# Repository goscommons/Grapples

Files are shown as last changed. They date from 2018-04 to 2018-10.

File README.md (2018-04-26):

# Welcome to this open source project
This repository has specific structure inspired in the [open hardware repository project structure guidelines](https://www.ohwr.org/projects/ohr-support/wiki/project-structure-guidelines). It has been also provided and organized by GO!Commons a community and initiative focused on the role of open source to accelerate sustainable development and deliver economic empower to producers, and commoners.

## About the structure and organization of the repository
The wiki is a very important part of the documentation structure of this repo. It will give you a quick introduction to the particularities of this design, how it is used, how it works, why it exists, but also the functional description of it etc.
### For users
If you are interested in understanding how this machine/product works, you can learn from reading the documentation. If you want to use the files in your projects, and make your own redesigns you are also welcome. Make sure to read the rights and attributions you have as a user in the [LICENSE.md](LICENSE.md).

### For contributors
If you want to learn open source by doing things, and you are interested in participating in this project in particular. Contact us or leave a comment on the #issues you are interested in participating. Some issues are for advanced developers others, are for beginners.

**don't be shy, we encourage that people partner up, and we also promote that experienced people play a mentor role so that others can grow as well**

#### You can see the different roles in the GO!Commons canvas, where we lay out the different roles that can participate. If you think your role is not captured or expressed, also feel free to reach out. You can also select the one that you fill more close to and start learning and finding your own contributor profile along the way.
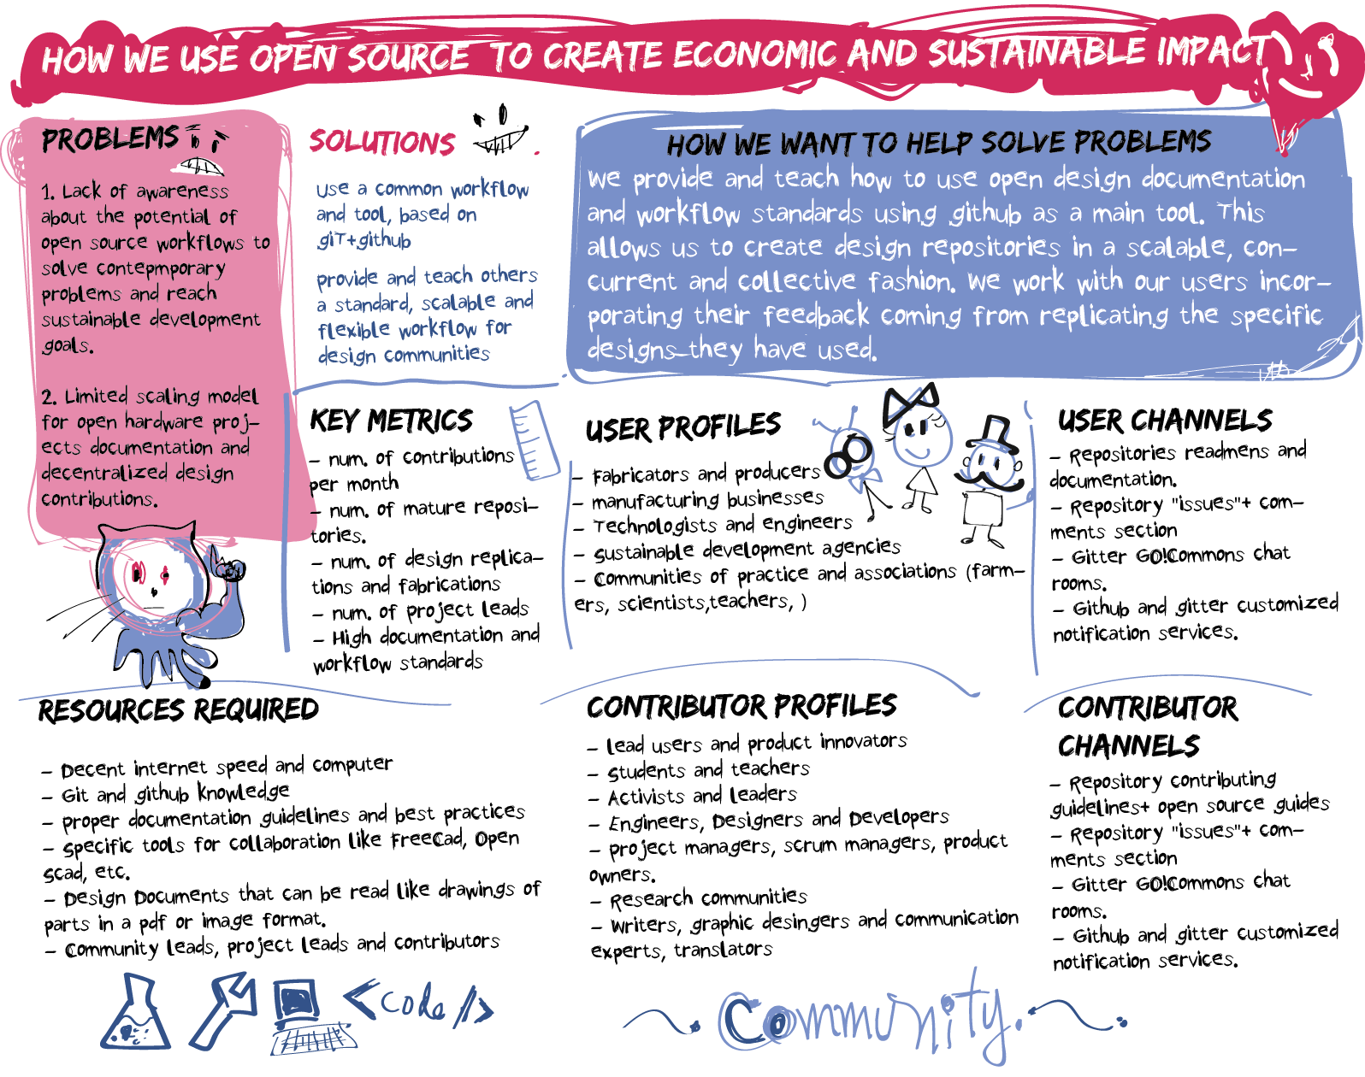
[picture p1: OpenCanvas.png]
GO!Commons Canvas


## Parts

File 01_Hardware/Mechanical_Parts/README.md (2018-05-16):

## What is the content in this folder and how to use it
The CAD structure is a diagram that allows you to understand different aspects of the design including:
* Dependencies and relations between parts.
* Fabrication related information like which parts will be manufactured with what process.
* Assembly and subassembly structures, very important to understand how to replicate the machine.
#[Find the link to the diagram here](https://drive.google.com/file/d/1CbiELoN1rX2ZCeMyn5z_mOmvfSASwcS_/view?ts=5af6c786). This will teach you how to also do similar kinds of diagrams.

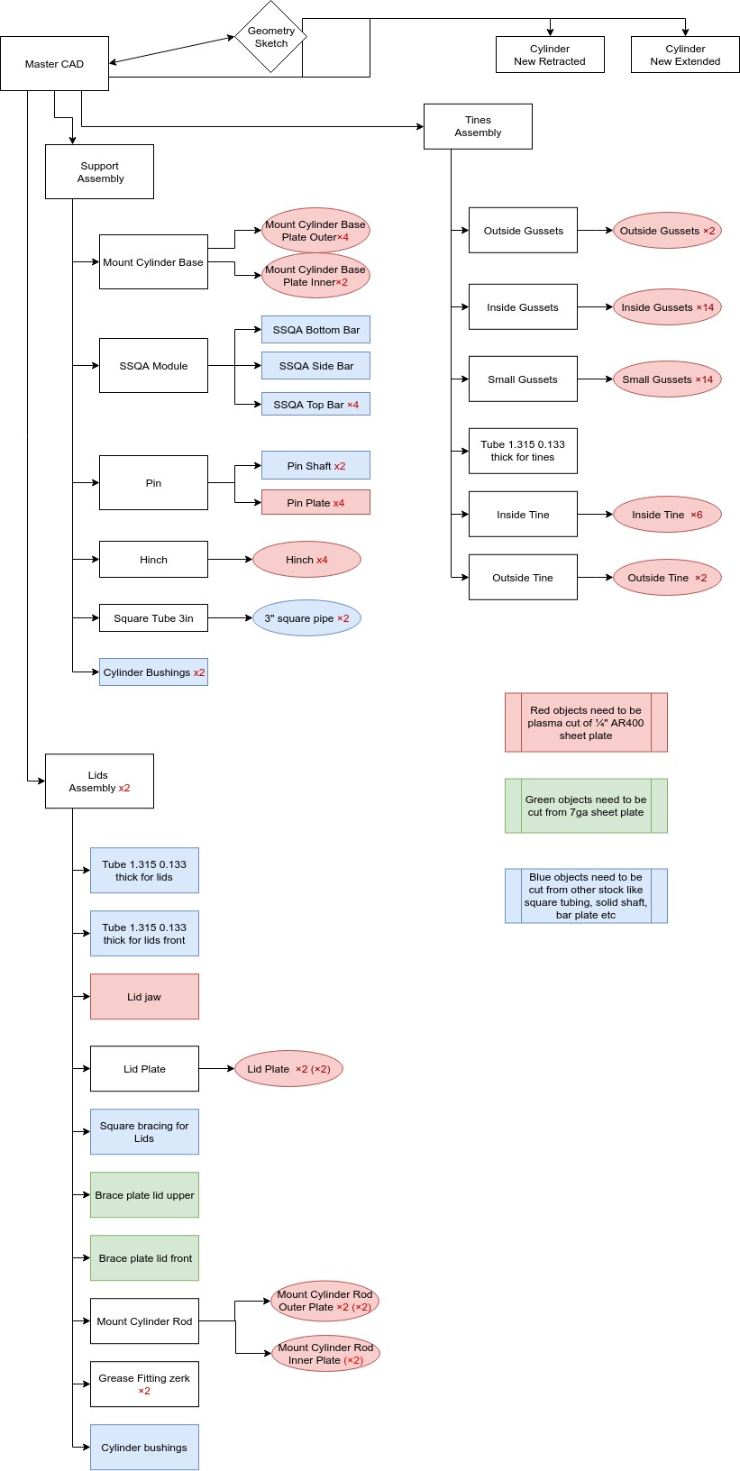
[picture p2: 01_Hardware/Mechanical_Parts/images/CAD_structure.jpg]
cad structure


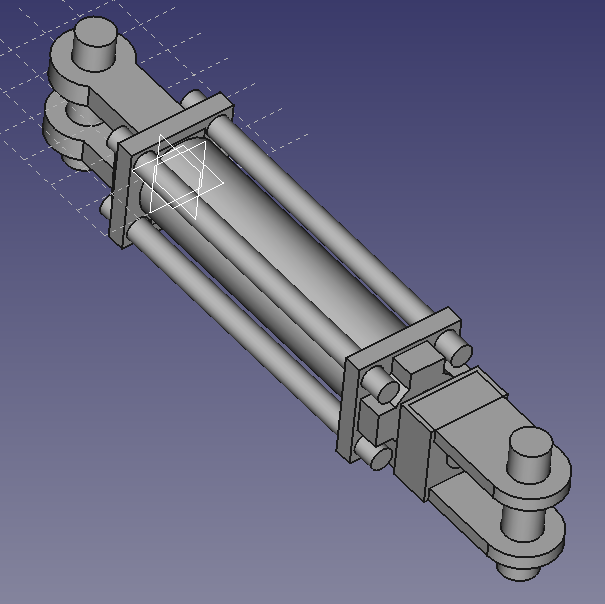
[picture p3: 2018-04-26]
01_Hardware/Mechanical_Parts/images/cylynder_retracted.png

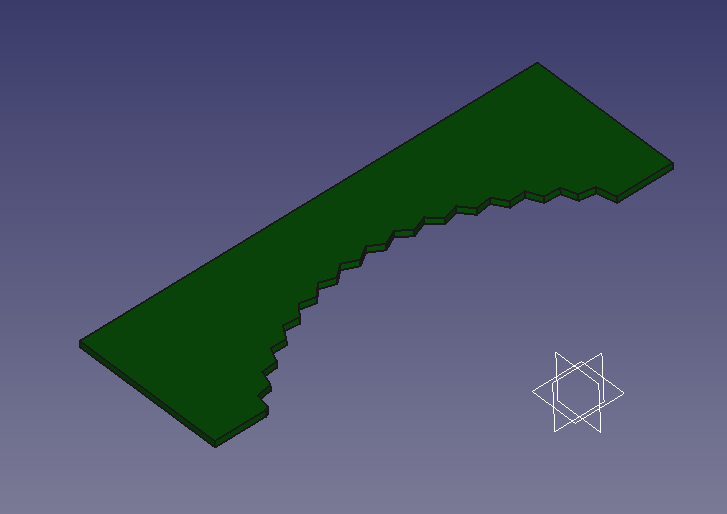
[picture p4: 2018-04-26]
01_Hardware/Mechanical_Parts/images/lid_jaw.png

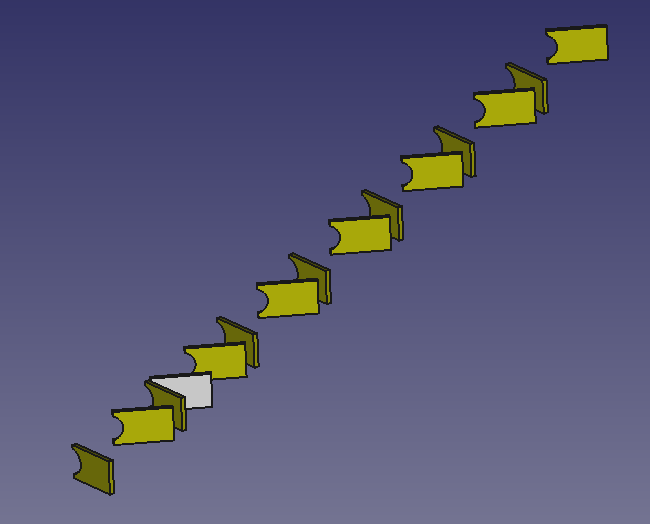
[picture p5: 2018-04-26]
01_Hardware/Mechanical_Parts/images/gussets.png

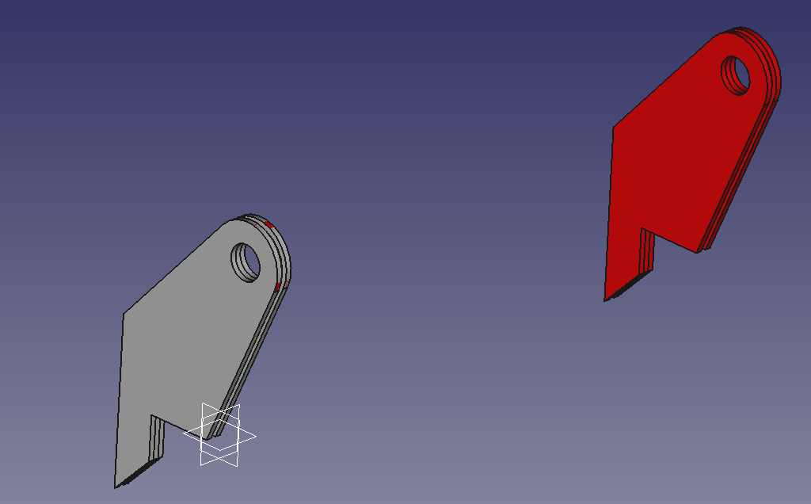
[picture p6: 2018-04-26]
01_Hardware/Mechanical_Parts/images/cylinder_base_mount.png

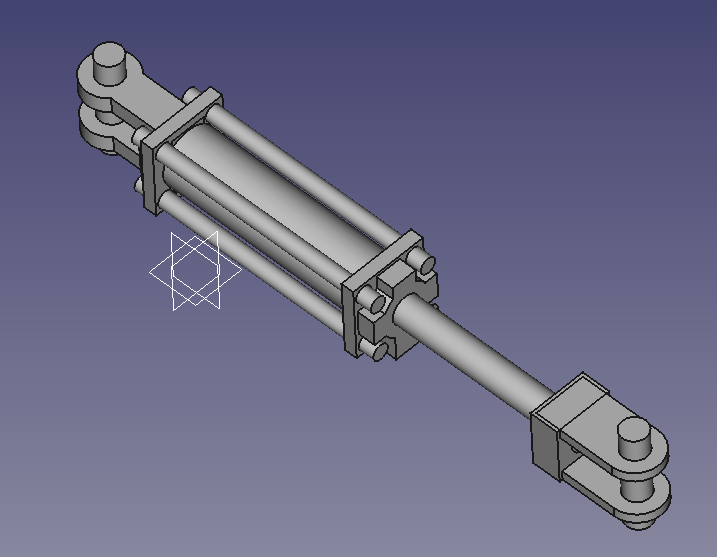
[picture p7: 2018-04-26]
01_Hardware/Mechanical_Parts/images/cylynder_extended.png

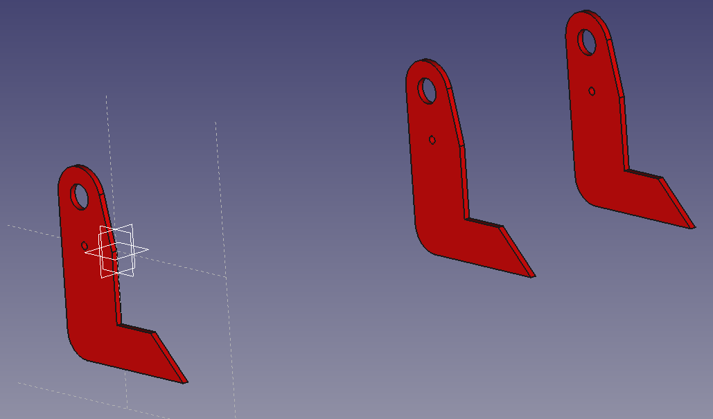
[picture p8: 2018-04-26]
01_Hardware/Mechanical_Parts/images/hinch.png

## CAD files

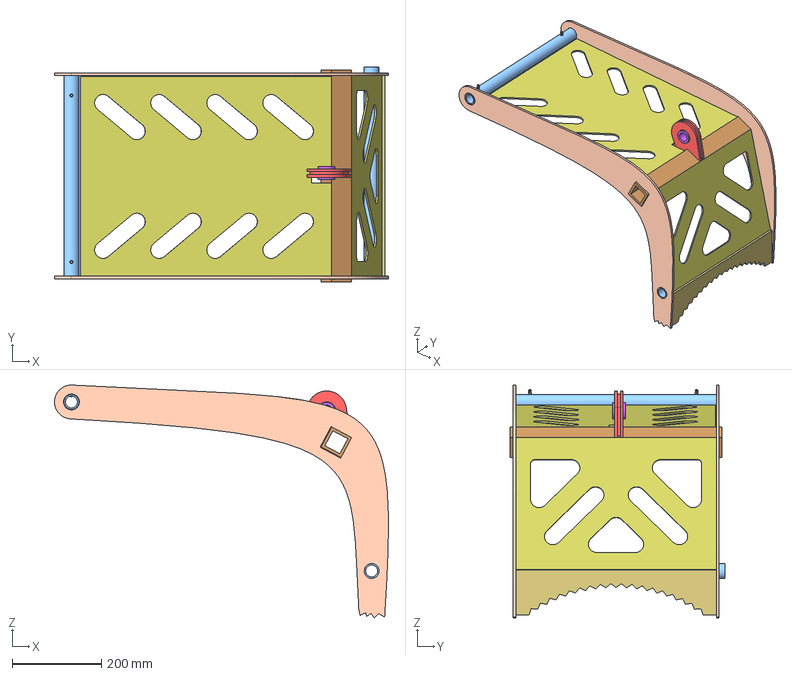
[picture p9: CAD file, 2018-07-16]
01_Hardware/Mechanical_Parts/CAD/Lids Assembly.fcstd
750.5 x 482.6 x 523.4 mm
Lid_jaw_01
Tube_1_315_0_133 thick_for_lids_01
Lid_Plate_01
Tube_1_315_0_133 thick_for_lids_front
Square_bracing_for_lids_01
brace_plate_lid_upper_01
brace_plate_lid_front_01
Cylinder_rod_mount_01
grease_fitting_zerk_01
grease_fitting_zerk_02
cylinder_bushings_01

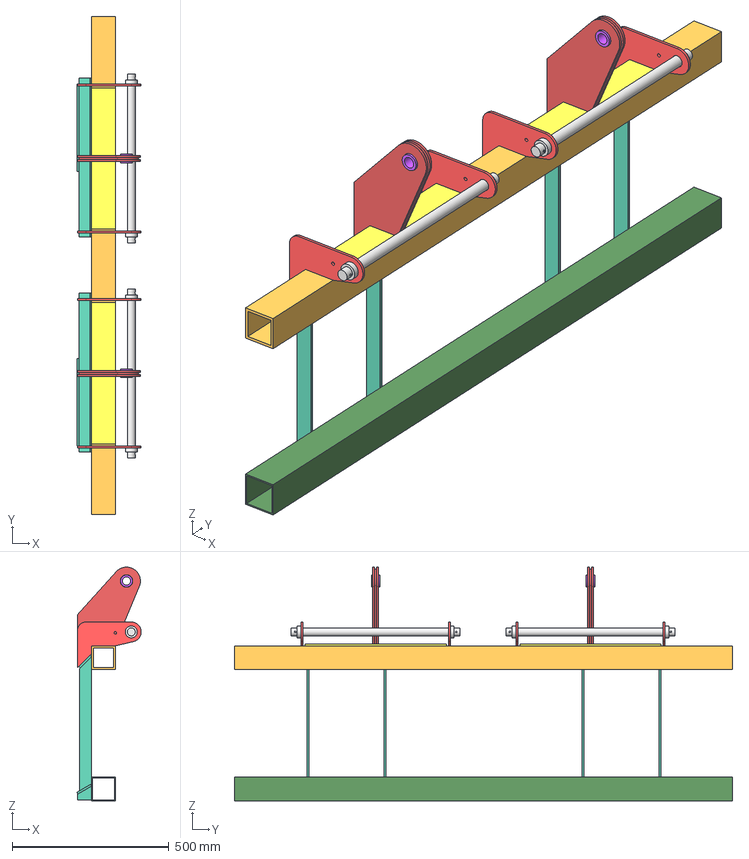
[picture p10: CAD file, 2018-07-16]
01_Hardware/Mechanical_Parts/CAD/Support Assembly.fcstd
205.9 x 1590.5 x 746.8 mm
mount_cylinder_base_01
ssqa_module_01
hinch_01
Square_tube_3in_01
bushings_for_cylinder_01
bushings_for_cylinder_02
pin_module_01
pin_module_02
Square_tube_3in_bottom_01
Support_plate_on_top_of_square_tubing_01

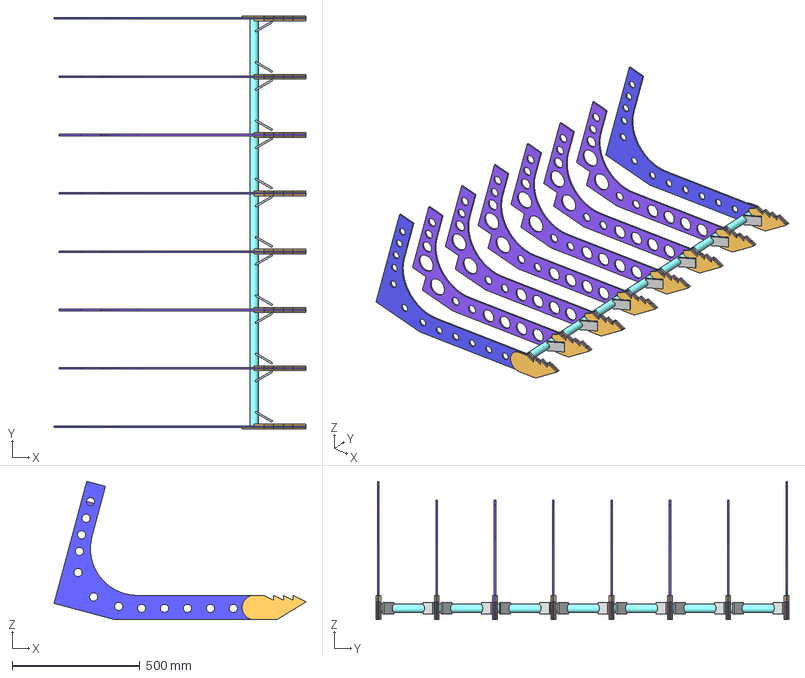
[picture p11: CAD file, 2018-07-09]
01_Hardware/Mechanical_Parts/CAD/Tines Assembly.fcstd
988.0 x 1619.2 x 542.4 mm
Inside gussets
gussets_02
Tube_1_315_0_133 thick_for_tines_01
Inside_tine_01001
Outside_Gussets_01
Outside_tine_01

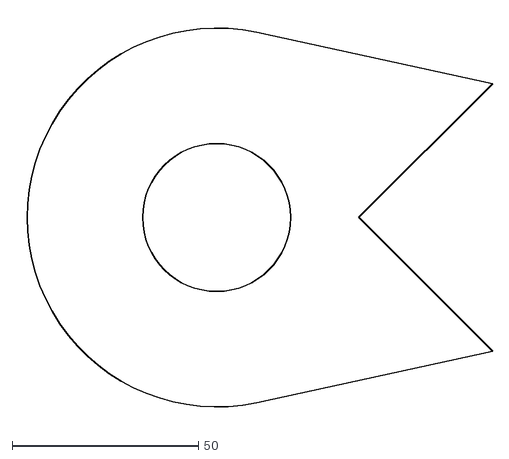
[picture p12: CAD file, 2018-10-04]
01_Hardware/Mechanical_Parts/CAD/Cuztomizable-Model/cylinder_rod_mount.dxf
127.7 x 108.1

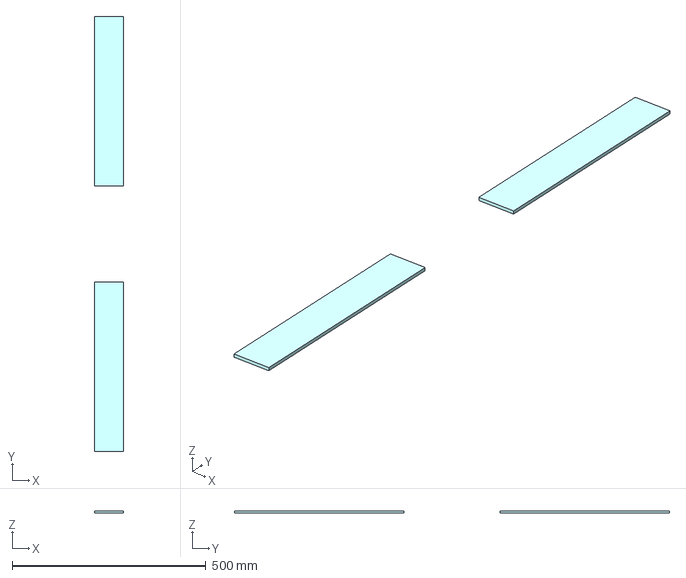
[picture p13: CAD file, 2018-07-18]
01_Hardware/Mechanical_Parts/CAD/Support plate on top of square tubing.fcstd
76.2 x 1123.9 x 6.35 mm

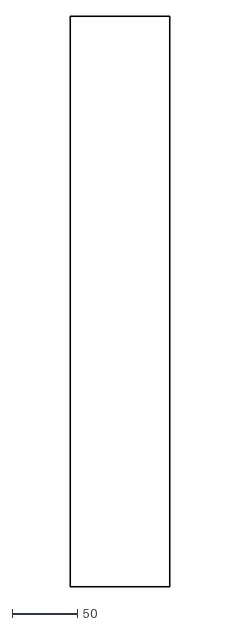
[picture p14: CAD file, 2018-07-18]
01_Hardware/Mechanical_Parts/fabrication/dxf-files/support plate on top of square tubing.dxf
76.2 x 438.1

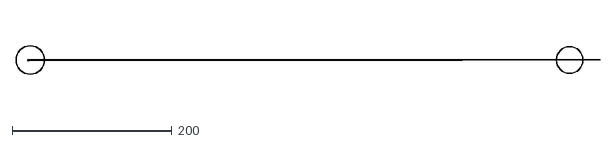
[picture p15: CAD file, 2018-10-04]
01_Hardware/Mechanical_Parts/CAD/Cuztomizable-Model/lid_plate_2.dxf
730.3 x 35.6

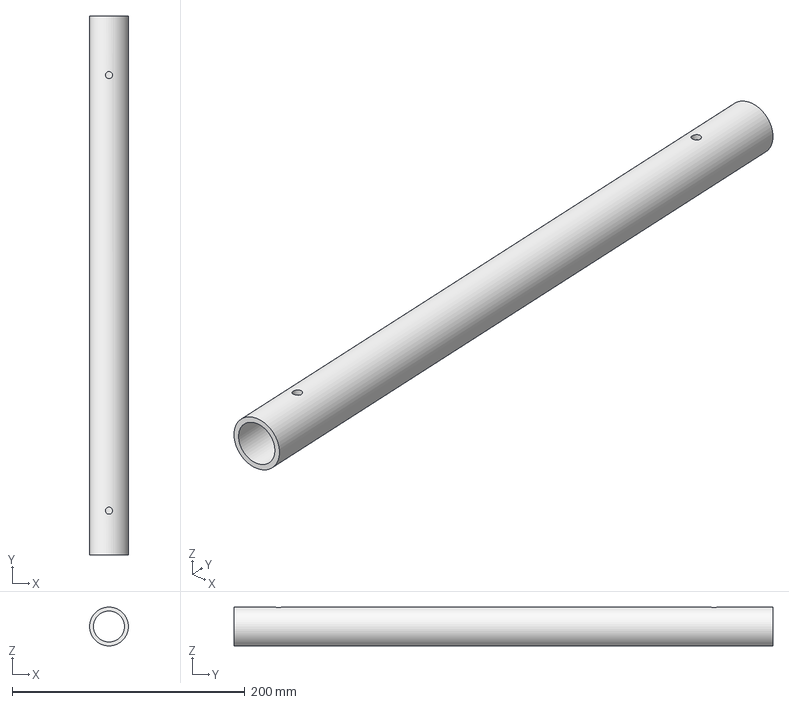
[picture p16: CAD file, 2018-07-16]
01_Hardware/Mechanical_Parts/CAD/Tube 1.315 0.133 thick for lids.fcstd
33.4 x 463.6 x 33.4 mm

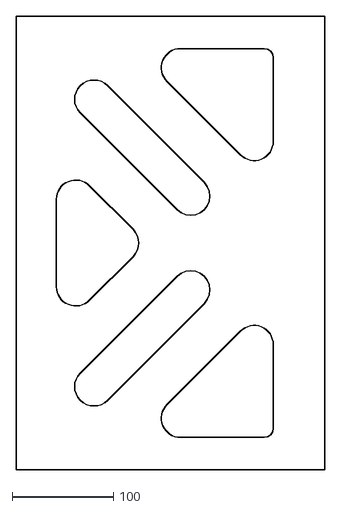
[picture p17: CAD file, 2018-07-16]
01_Hardware/Mechanical_Parts/fabrication/dxf-files/brace plate lid front.dxf
304.8 x 448.3

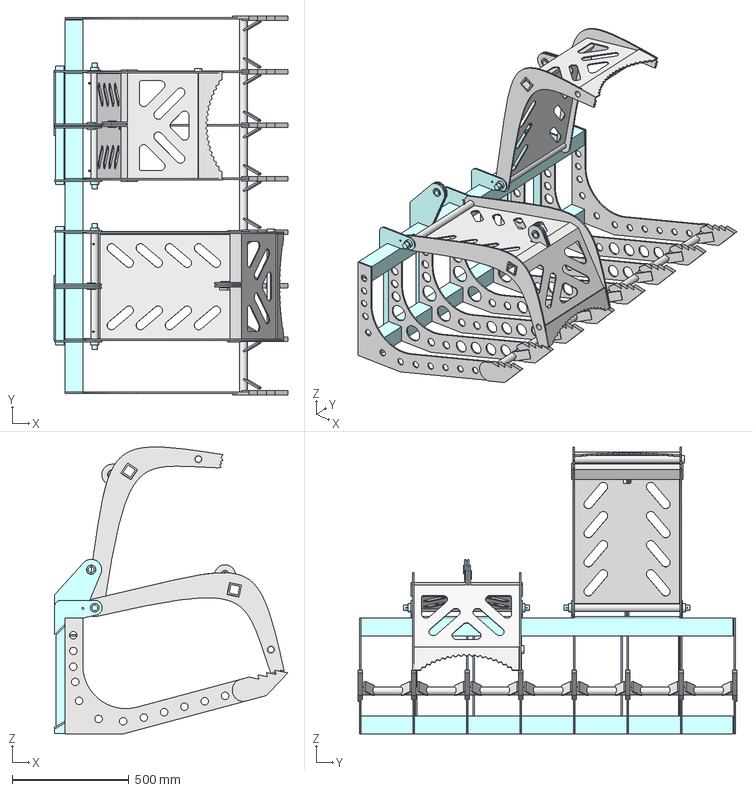
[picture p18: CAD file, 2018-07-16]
01_Hardware/Mechanical_Parts/CAD/0-Master CAD.fcstd
1000.0 x 1619.3 x 1226.8 mm
Support_Assembly_01
Tines_Assembly_01
Lids_Assembly_01
Lids_Assembly_02

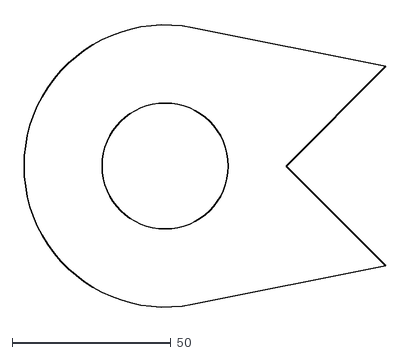
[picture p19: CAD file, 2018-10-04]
01_Hardware/Mechanical_Parts/CAD/Cuztomizable-Model/cylinder_rod_mount_in.dxf
116.5 x 94.2

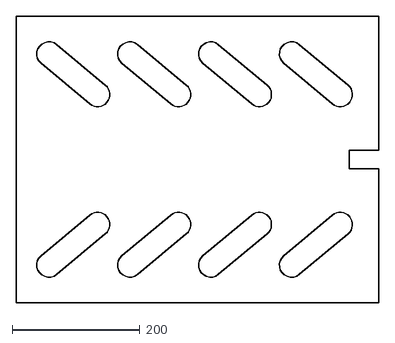
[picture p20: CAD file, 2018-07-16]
01_Hardware/Mechanical_Parts/fabrication/dxf-files/brace plate lid upper.dxf
566.4 x 448.3

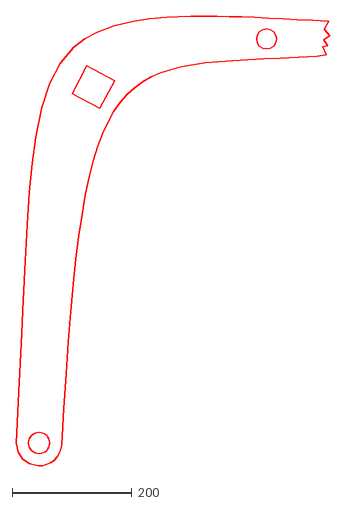
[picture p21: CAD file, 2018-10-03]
01_Hardware/Mechanical_Parts/CAD/Cuztomizable-Model/lid_plate.dxf
523.4 x 750.6

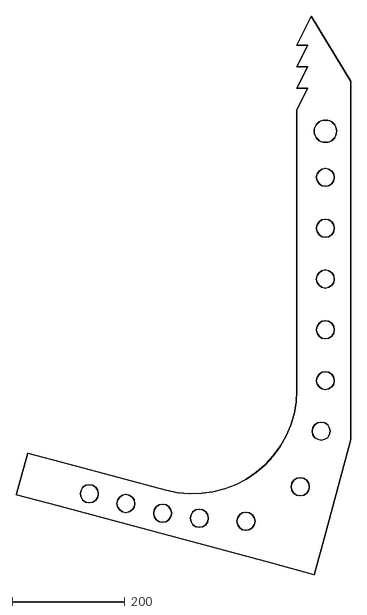
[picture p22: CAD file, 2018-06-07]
01_Hardware/Mechanical_Parts/fabrication/dxf-files/outside tine.dxf
591.5 x 988.0

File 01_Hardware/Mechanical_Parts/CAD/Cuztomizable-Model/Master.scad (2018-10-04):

// INDEPENDENT VARIABLES
/* Tynes Subassemblies parameters*/
l=1200;// width of grapples
tynes_num=10;//ammmount of inner tynes
sh_thick=10; // Sheet thickness

/*Lid Parameters*/
l_lid=520;

// DEPENDENT VARIABLES**DON'T CHANGE**
d_b_tynes=l/tynes_num;// distance between tynes recalculation
l_ratio=(l_lid-l_lid*0.07)/450;// Recalculation of front and up plate based on original size


module tynes(){
color("red"){
translate([-sh_thick,0,0])rotate([0,90,0])linear_extrude(center=true,  height = sh_thick)import (file = "ingussets.dxf");

}

translate([-410,100,25])
rotate([0,90,-30])linear_extrude(center=true,  height = sh_thick)import (file = "gussets.dxf");

rotate([0,90,0])linear_extrude(center=true,  height = sh_thick)import (file = "outsidetine.dxf");

}

/* tynes(); */
/*Support Assembly
- [] mount cylinder base 01
- [] ssqa_module
- [] hinch 01
- [] Bussings for Cylinder 01
- [] Bushings for Cylinder 02
- [] pin 1
- [] pin 2
- [] Support plate on to of square tubing
*/

module hinch(){
rotate([0,90,0])linear_extrude(center=true,  height = sh_thick)import(file="hinch.dxf");

}

module mount_cylinder(){
		for (i=[0:4]) {
		translate([i*(sh_thick+sh_thick*0.1)-sh_thick*2, 0, 0])rotate([0,90,0])linear_extrude(center=true,  height = sh_thick)import(file="mount_cylinder.dxf");
	}

}

// Square tube
module sq_tube(length,size){
	/* difference() {
		cube([l,sq_tb*(24.5),sq_tb*(24.5)], center=true);
		cube(size=[l+l*0.2, sq_tb*(24.5)-15, sq_tb*(24.5)-15], center=true);
 	} */

	difference(length,size) {
		cube([length,size*24.5,size*24.5], center=true);
		cube([length+length*0.2, size*(24.5)-15, size*(24.5)-15], center=true);
	}
}


module in_tynes(){
	rotate([0,90,0])
	linear_extrude(center=true,  height = sh_thick)
	import(file="insidetine.dxf");
	color("red"){
	translate([-sh_thick,0,0])rotate([0,90,0])linear_extrude(center=true,  height = sh_thick)import (file = "ingussets.dxf");
	translate([sh_thick,0,0])rotate([0,90,0])linear_extrude(center=true,  height = sh_thick)import (file = "ingussets.dxf");

	translate([415,115,30])
	rotate([0,90,30])linear_extrude(center=true,  height = sh_thick)import (file = "gussets.dxf");
	mirror([1,0,0]){
	translate([405,115,30])
	rotate([0,90,30])linear_extrude(center=true,  height = sh_thick)import (file = "gussets.dxf");
	}
	}
}

/* in_tynes(); */
module tube(r,lng,th){
/* difference(){
	cylinder(r=17, h=l, center=true);
	cylinder(r=15, h=l+l*0.2, center=true);
	} */
	difference(){
		cylinder(r=r, h=lng, center=true);
		cylinder(r=r-th, h=lng+lng*0.2, center=true);
		}
}

translate([l/2,710,44])
color("white")
rotate([0,90,0])
tube(17,l,3);


module integration(){
// Square tube bottom
translate([-sh_thick*2,-20,40]){
translate([sh_thick*2+l/2,0,50])rotate([75,0,0])color("yellow")
// Squre tube top
sq_tube(l,3);

for (i=[0:1]) {
	translate([i*l/2,0,0]){
	color("green"){
	rotate([-15,0,0])translate([l/3.75+l_lid/2,-55,420])hinch();
	rotate([-15,0,0])translate([l/3.75-l_lid/2,-55,420])hinch();
	rotate([-15,0,0])translate([l/3.75,-55,420])mount_cylinder();
	}
	}
}


translate([sh_thick*2+l/2,105,450])rotate([75,0,0])color("blue")
sq_tube(l,3);
}

translate([d_b_tynes,0,0])for (i=[0:tynes_num-2])
   translate([i*d_b_tynes,0,0])
	 // Replace this by a module
     /* rotate([0,90,0])linear_extrude(center=true,  height = sh_thick)import(file="insidetine.dxf"); */
		 in_tynes();

translate([l,0,0])tynes();
mirror([1, 0, 0]) {
	translate([0,0,0])
	tynes();
	}
}

integration();


/*Lids subassembly*/
module lids_assem(){
module lids(){
/* - [] thickness space, coupling connection
*/
module lid_plate(){
translate([0,0,700])rotate([0,90,0])linear_extrude(center=true,  height = sh_thick)import (file = "lid_plate.dxf");
}
translate([l_lid/2-sh_thick*1.3,0,0])
lid_plate();
mirror(){
	translate([l_lid/2-sh_thick*1.3,0,0])
	lid_plate();
	}
}

module up_plate(){
	linear_extrude(height = sh_thick)import (file = "brace_plate_lid_upper.dxf");
}

module front_plate(){
	linear_extrude(height = 10)
	import (file = "brace_plate_lid_front.dxf");
}

module lid_jaw(){
	linear_extrude(height = 10, center=true)
	import (file = "lid_jaw.dxf", center=true);
}

module rod_mount(args) {
	translate([0,0,sh_thick])
	linear_extrude(height = sh_thick)
	import (file = "cylinder_rod_mount.dxf");
	color("red")
	linear_extrude(height = sh_thick)
	import (file = "cylinder_rod_mount_in.dxf");
	translate([0,0,-sh_thick])
	linear_extrude(height = sh_thick)
	import (file = "cylinder_rod_mount.dxf");
}



for (i=[0:1]) {
	translate([i*l/2,0,0])
color("yellow"){
/*lids subassembly
- [] busshings
- [x] cylinder mount
*/
translate([l/4,767,493])
rotate([12,0,0])
rotate([0,90,0])
rod_mount();


translate([l/4,856,160])
rotate([90,0,90])
tube(20,l_lid,3);

translate([l/4,189,548])
rotate([90,0,90])
tube(15,l_lid,3);

translate([l/4,880,-220])
rotate([0,90,90])
scale([1,l_ratio,1])
lid_jaw();

translate([l/4,181,-155])
lids();

translate([l/4,205,540])
rotate([-6, 0, 0])
rotate([0,0,90])
scale([1,l_ratio,1])
up_plate();

translate([l/4,865,210])
rotate([-77,0,0])
rotate([0,0,270])
scale([1,l_ratio,1])
front_plate();


translate([l/4-l/4*0.05,780,450])
rotate([62,0,0])
sq_tube(l_lid-l_lid*0.05,2.2);
		}
	}
}

lids_assem();

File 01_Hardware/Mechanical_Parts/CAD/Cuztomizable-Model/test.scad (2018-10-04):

l=600;
l_ratio=l/450;

/* cube([20,450,10], center=true); */
module plato(args) {
	linear_extrude(height = 10)
	import (file = "cylinder_rod_mount_in.dxf");
}

scale([1,1,1])plato();

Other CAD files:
01_Hardware/Mechanical_Parts/fabrication/master-cad.DWG
01_Hardware/Mechanical_Parts/CAD/Cuztomizable-Model/lid_jaw.dxf
01_Hardware/Mechanical_Parts/CAD/ssqa module.fcstd
01_Hardware/Mechanical_Parts/fabrication/dxf-files/inside tine.dxf
01_Hardware/Mechanical_Parts/CAD/Cuztomizable-Model/brace_plate_lid.dxf
01_Hardware/Mechanical_Parts/CAD/Cuztomizable-Model/brace_plate_lid_front.dxf
01_Hardware/Mechanical_Parts/CAD/Cuztomizable-Model/brace_plate_lid_upper.dxf
01_Hardware/Mechanical_Parts/CAD/Cuztomizable-Model/gussets.dxf
01_Hardware/Mechanical_Parts/CAD/Cuztomizable-Model/hinch.dxf
01_Hardware/Mechanical_Parts/CAD/Cuztomizable-Model/ingussets.dxf
01_Hardware/Mechanical_Parts/CAD/Cuztomizable-Model/insidetine.dxf
01_Hardware/Mechanical_Parts/CAD/Cuztomizable-Model/mount_cylinder.dxf
01_Hardware/Mechanical_Parts/CAD/Cuztomizable-Model/outgussets.dxf
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

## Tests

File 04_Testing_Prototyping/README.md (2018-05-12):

The link for the Grapple CAD Structure.png is https://drive.google.com/file/d/1CbiELoN1rX2ZCeMyn5z_mOmvfSASwcS_/view?usp=sharing

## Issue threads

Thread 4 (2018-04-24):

Round tubings have to be changed

polemidis, 2018-04-24:
The plan currently utilizes Drive Over Mandrel Tubing. After I got quotes for this product, I found it inefficient to use it as it defies the purpose of this design: It is very very expensive. About 9x times more than a conventional round tube.
So I got in hand the 1" (nominal size) pipe, and fits perfectly over the 1" solid shaft. This pipe is 1.315"OD with 0.133" wall, leaving 1.049 ID (just over 1") so the weld on the inside of the pipe does not interfere with the 1" solid shaft.
On the CAD:
The pipes, bushings and parts that have bushings have to be updated

Closed 2018-05-12.

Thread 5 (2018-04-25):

Complete parts and assembly wiki section

jurra, 2018-04-25:
Some of this tasks can be left for other contributors like @memeco so that they can have room to do one of the documentation tasks

-[ ] Download files, and open them of freeCAD @jurra
-[ ] Take pictures of each part and upload them in the repo @jurra
-[ ] Take pictures of the general assembly
-[ ] Make a table in markdown with the different parts pointing to the file url on the repo #mozsprint

polemidis, 2018-05-16:
I believe we have all the pictures of the parts taken, right? Then we can close this issue too?

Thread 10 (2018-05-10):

hydraulic cylinder technical drawing

goscommons, 2018-05-10:
[File](https://github.com/goscommons/Grapples/blob/master/01_Hardware/Mechanical_Parts/), [image](https://github.com/goscommons/Grapples/blob/master/01_Hardware/Mechanical_Parts/images/cylynder_extended.png)

Most important in this case are the dimensios of the cylinder, and specially those related to other parts like the link

polemidis, 2018-05-11:
The cylinder I put in the cad is there just in order to calculate the geometries of closed/ open position. Different brands of cylinder are not important. Not even different types. The one in the drawing is a tie-rod cylinder, but a welded cylinder could be used as well.
As such the above is 2" dia meter cylinder, but I propose that a 2.5" diameter cylinder should be used.

polemidis, 2018-05-12:
To make things easier about the cylinder. Its specs are:
Cylinder retracted length from center to center of pins: 16.25"
Cylinder extended: 22.25"

They are common 2"(bore dia) x 6"(stroke length) dimension cylinders, like [these](https://www.surpluscenter.com/Hydraulics/Hydraulic-Cylinders/Double-Acting-Hydraulic-Cylinders/2x6x1-125-DA-Hydraulic-Cylinder-W200060-S-9-8534-6.axd)

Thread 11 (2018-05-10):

[1.0] Mapping Grappler's components

goscommons, 2018-05-10:
Goal: Identifying different components part of the Grapper

- [x]  - Identify resources and reference materials i.e. diagrams
- [x] - Create documentation on .txt for all identified components

polemidis, 2018-05-16:
We could close this one too, the tree diagram covers this issue right?
Btw the diagram is edible :) its not just a picture

Closed 2018-05-16.

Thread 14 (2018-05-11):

1st. Step: Preparing tech-drawing tasks, and setting up the tools you need to work in this sprint

goscommons, 2018-05-11:

polemidis, 2018-05-11:
A note in Freecad (it should go somewhere more visible). You need to add the Assembly 2 workbench,  The "Master CAD" is the... master cad file :) that includes the assemblies. Some assemblies are made of other sub-assemblies. Unfortunately -for now- the files' location is absolute, meaning that as soon as you download them in your computer it will be different that my location. However the "Update" button in that workbench will recognize the new folder structure. It does take a few minutes though :(

Also check out this [link](https://www.everythingattachments.com/Wicked-Root-Grapple-by-Everything-Attachments-p/eta-wrg-cmp.htm) The videos shows everything about the grapple. Our grapple is very similar to that one ;)

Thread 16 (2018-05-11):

[2.0] Dimension of Key Components

cls-c, 2018-05-11:
Designing the dimension of key components of Grapple

- [ ] Identifying Customers needs/ Requirement
- [ ]  Research for standard dimensions based on the existing market products
- [ ]  Design and document key dimension for each identified component

goscommons, 2018-05-11:
Hi cls-c we already have all these, you have them on your machine as CAD models.
If you see the hydraulic cylincer issue, or the clamp issue, those are examples of components to be documented, using the cad models. See the example of a card finished done by @krishnarajagopal2011 [Task breakdown and deliverable example](https://github.com/goscommons/Grapples/issues/12)

jurra, 2018-05-13:
Hi @cls-c this issue, is not making sense at the moment. I am going to close, you can still see it though, to reflect on what you were trying to achieve. But keep in mind that the goal of this sprint is to document already existing parts, so that others can see the technical documentation without having to open a CAD. I allows also fabricators to consider, proper parts dimensions etc.

Closed 2018-05-13.

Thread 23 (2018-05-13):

Tynes_Assembly_02

goscommons, 2018-05-13:

jurra, 2018-05-13:
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

I figured out this another assembly we should be documenting. The one above is a sub-assembly. @polemidis how do we go ahead with thsi, do we have to make a CAD for the subassembly. Do we have that CAD model?

polemidis, 2018-05-13:
I don’t get what you mean Jose :(

Sent from my iPhone

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

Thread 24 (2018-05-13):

Idea: protocol for assembly steps documentation

jurra, 2018-05-13:
It can be useful to consider the order of assembly steps in the structure of the cad file, this way we can already know the order of assembly. I put an example of how it can be. In this case the order might be wrong, I just make the point of putting numbers infront of the item names, that show already the order of assembly, This can work in the master cad as well as in subassemblies.
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

Maybe the structure of folders could be improved, since now all the parts are together with assembly names. Maybe just putting an A,(Assembly); P (Part) ;(C) Off the shelve component infront of names of files can also help. AA for subassembly first level?

For instance AA_Tynder_Assembly; A_Grapples; C_Hydraulic_Cylinder; etc.

polemidis, 2018-05-13:
Something that seperates the simple parts from the assemblies would be nice. But some parts belong to multiple assemblies. I think that the current names, with the name tree is sufficient. It’s different to make a few name changes if something is not clear and different to rename every part, change every link on that part on the assembly, and change the description of that part. LOTS of work for no clear benefit, which more than likely it will break up everything, because users are not familiar with the Freecad

polemidis, 2018-05-13:
But what definitely has to be done in order to go forward with this project is to make .svg or .dxf files of every part that has to be cut in plasma ( all flat parts ). My plasma is ready to cut, I have the air drier set up. Once cut we can have real pictures, see real issues that may slip the CAD detection

polemidis, 2018-05-13:
And lastly, because that’s a done cad model, if you want to organize , test the cad creation procedure, which is the actual fun :) what about work on the plasma model, that has cad needs? I mean that’s the backbone of every project, and people did not experience this in the grapple because it was already made

jurra, 2018-05-13:
Agree. Understand what you mean.

On Sun, May 13, 2018, 15:13 Manolis Karamousas <notifications@github.com>
wrote:

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

Closed 2018-05-16.

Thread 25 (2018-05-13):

generate svg files of pars that will be cutted with plasma

jurra, 2018-05-13:
List here laser cut metal parts

polemidis, 2018-05-15:
Jose I moved back in "In progress". There are some parts missing. I will work on that tonight. And document what is the best way to do the SSQA in the picture above

polemidis, 2018-05-15:
there should be 13 files. I will check it later. Or 11 with 2 files having
2 svg paths

On Tue, May 15, 2018 at 5:21 PM, Jose Carlos Urra Llanusa <
notifications@github.com> wrote:

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

--
Emmanouil Karamousadakis
Certified Permaculture Designer
AGreekulture Farmstead
Winthrop, ME 04364

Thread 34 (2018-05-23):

Design Optimization of Mechanical Parts

jurra, 2018-05-23:
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

I collect the comments from the chat discussions, to then document better the issue:

> Weight is the big limiting factor.
> SO my goals were a) to use lighter material b)to remove material from wherever I could without compromising strength

polemidis, 2018-08-09:
After using the grapple for a while I realized that there is no need for that calculation. The reason is that the tine is never in such angle as the analysis shows. Even though when I tried it for testing reasons, the bump is absorbed by the tractor.

However there is analysis needed on the closing action of the lids. If the grapple is uneven loaded, when the cylinder pushes the lid it deforms. I have not pushed it to the limit but I am not sure that the lid will hold.

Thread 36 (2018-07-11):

Assembly documentation, technical drawings grapples (Vinay)

jurra, 2018-07-11:
Making technical drawings that explain the fabrication process. In particular the assembly of the Grapples.

## First verify that the design is ready for documentation.
Is there something that needs to be done prior to this @polemidis?

polemidis, 2018-07-11:
Let me push the latest changes. Some minor details have changed. And I need to review the design. Will do it tonight

vinaybhajantri, 2018-07-24:
I'm almost ready with the drawings that I did in Solidworks but need to remove the watermarks etc. I'll do that with illustrator may be. But it is good to note, it is mainly meant to communicate not edit. We'll look into FreeCAD drawings next for editable version.

vinaybhajantri, 2018-08-03:
You should find the drawings [here](https://github.com/goscommons/Grapples/tree/master/01_Hardware/Mechanical_Parts/fabrication) in fabrication folder.

vinaybhajantri, 2018-08-03:
Main conclusion / learning from this task-

1. We definitively need to move to FreeCAD drawings, so I'm aiming to finish the svg icons this week so that we are capable of making production ready drawings.

2. When I import step files from FreeCAD, I loose lot of editable data like holes, some surfaces which make drawings difficult in SW. So not a good idea at all.

3. We should discuss the table that I have adapted from SW at bottom-right corner. Just to align ourselves on what all those things mean.

jurra, 2018-08-03:
Beautiful man!! Next the pull request should come, to have Manolis peer
review right?

On Fri, Aug 3, 2018 at 11:57 AM, Vinay Bhajantri <notifications@github.com>
wrote:

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

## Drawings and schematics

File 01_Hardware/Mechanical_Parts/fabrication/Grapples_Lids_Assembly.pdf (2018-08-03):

x 2

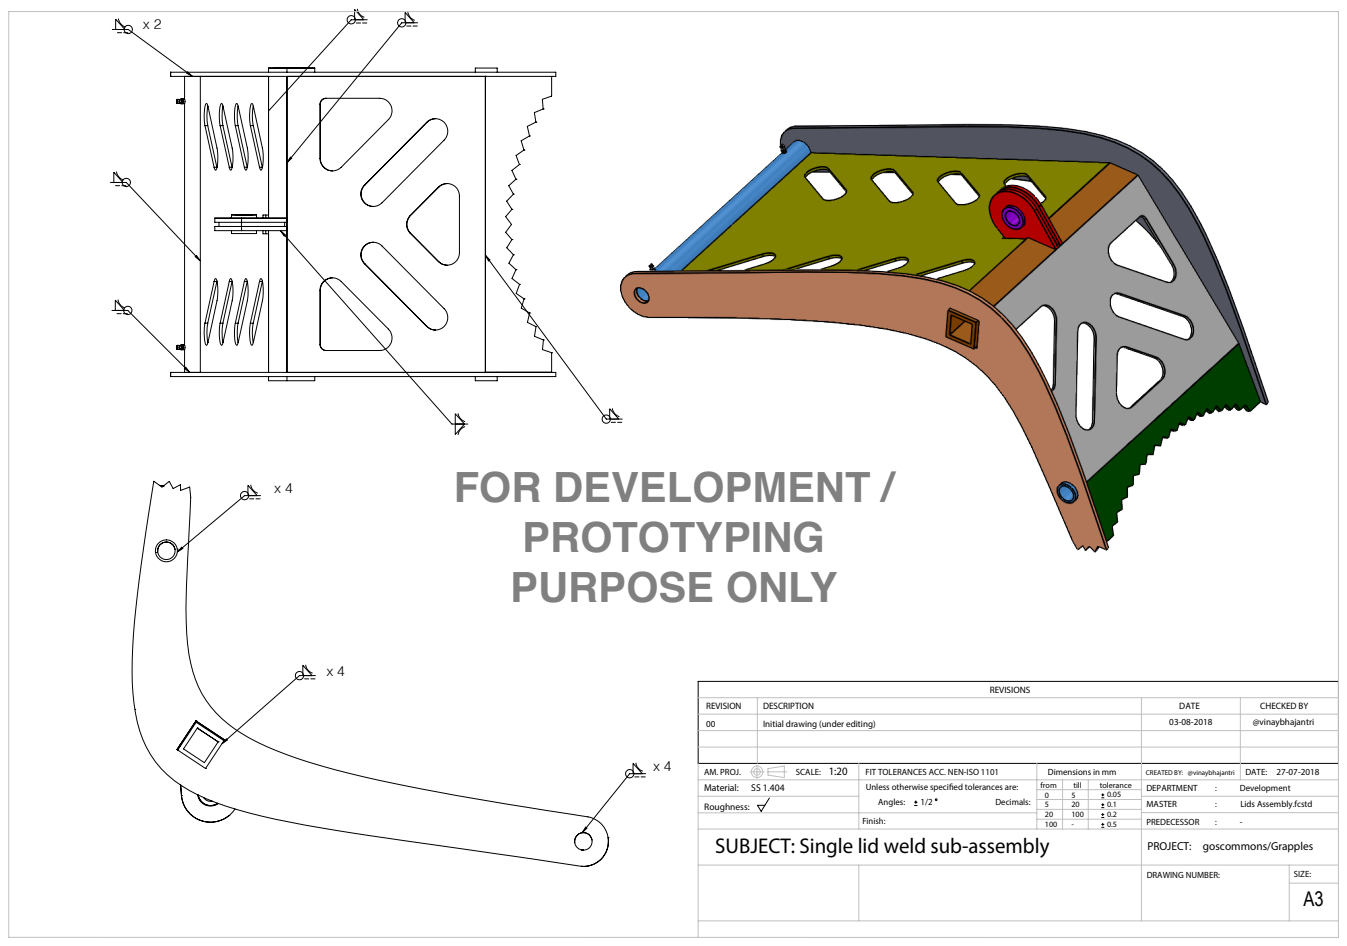
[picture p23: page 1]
CHECKED BY @vinaybhajantri; @vinaybhajantri; DATE 03-08-2018; REVISION; REVISIONS; SUBJECT: Single lid weld sub-assembly; PROJECT: goscommons/Grapples; Material: SS 1.404; SIZE: A3; DATE:; DRAWING NUMBER:; AM. PROJ.; FIT TOLERANCES ACC. NEN-ISO 1101; Dimensions in mm; CREATED BY:; Decimals:; from; till; tolerance; 0.5 Finish:; DEPARTMENT; Development; Roughness:; PREDECESSOR; SCALE: 1:20; MASTER; Lids Assembly.fcstd; FOR DEVELOPMENT / PROTOTYPING PURPOSE ONLY

DESCRIPTION
Initial drawing (under editing)

Unless otherwise specied tolerances are:
Angles:

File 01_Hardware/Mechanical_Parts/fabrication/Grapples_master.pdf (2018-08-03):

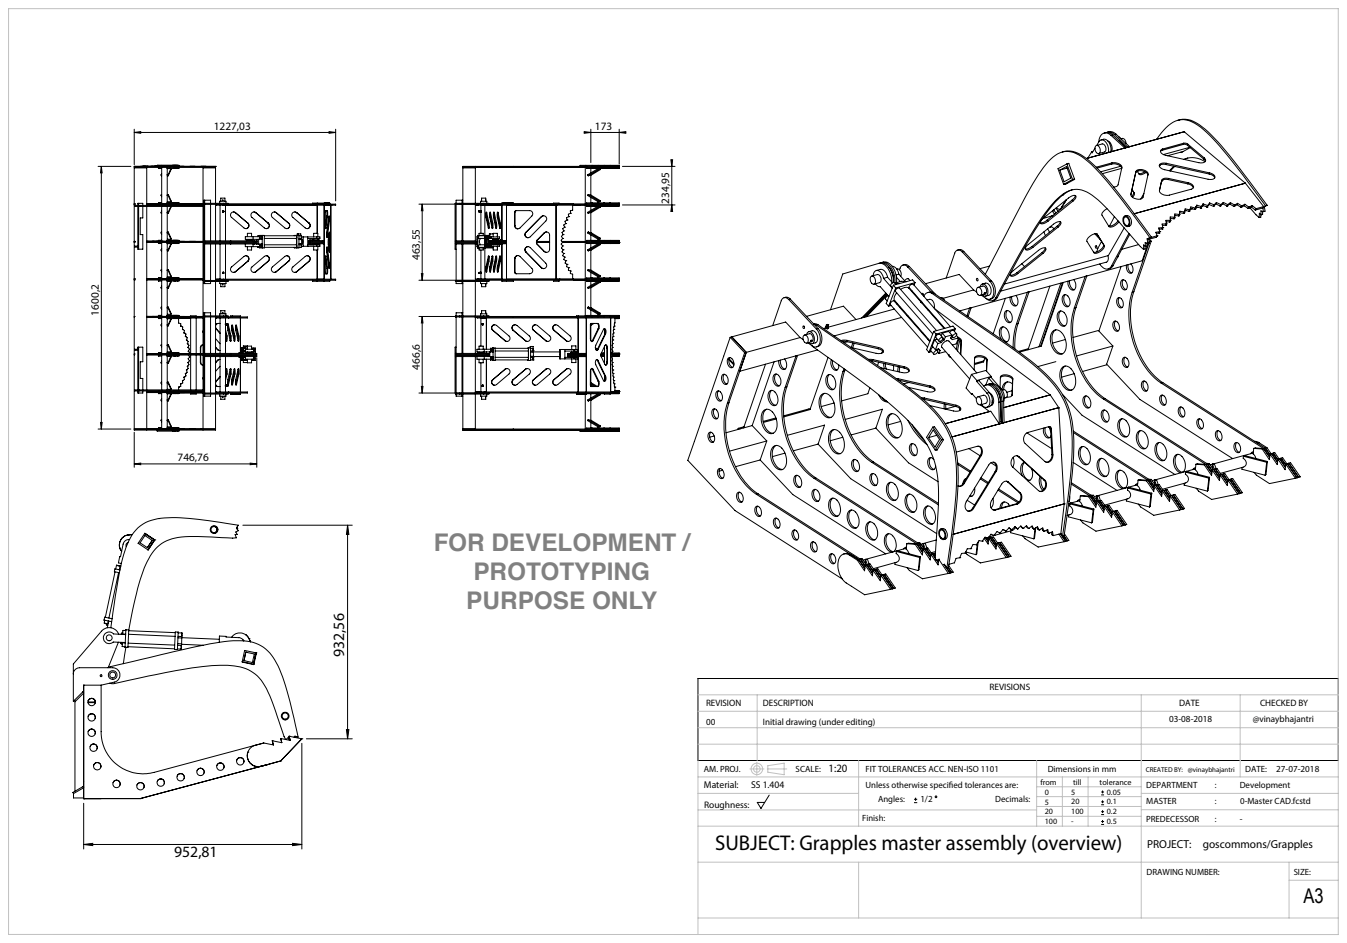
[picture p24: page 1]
CHECKED BY @vinaybhajantri; @vinaybhajantri; DATE 03-08-2018; REVISION; REVISIONS; SIZE: A3; DATE:; DRAWING NUMBER:; AM. PROJ.; FIT TOLERANCES ACC. NEN-ISO 1101; Dimensions in mm; CREATED BY:; Decimals:; from; till; tolerance; 0.5 Finish:; DEPARTMENT; Development; PREDECESSOR; SCALE: 1:20; MASTER; 0-Master CAD.fcstd; FOR DEVELOPMENT / PROTOTYPING PURPOSE ONLY

DESCRIPTION
Initial drawing (under editing)

Material: SS 1.404
Roughness:
SUBJECT: Grapples master assembly (overview) PROJECT: goscommons/Grapples

Unless otherwise specied tolerances are:
Angles:

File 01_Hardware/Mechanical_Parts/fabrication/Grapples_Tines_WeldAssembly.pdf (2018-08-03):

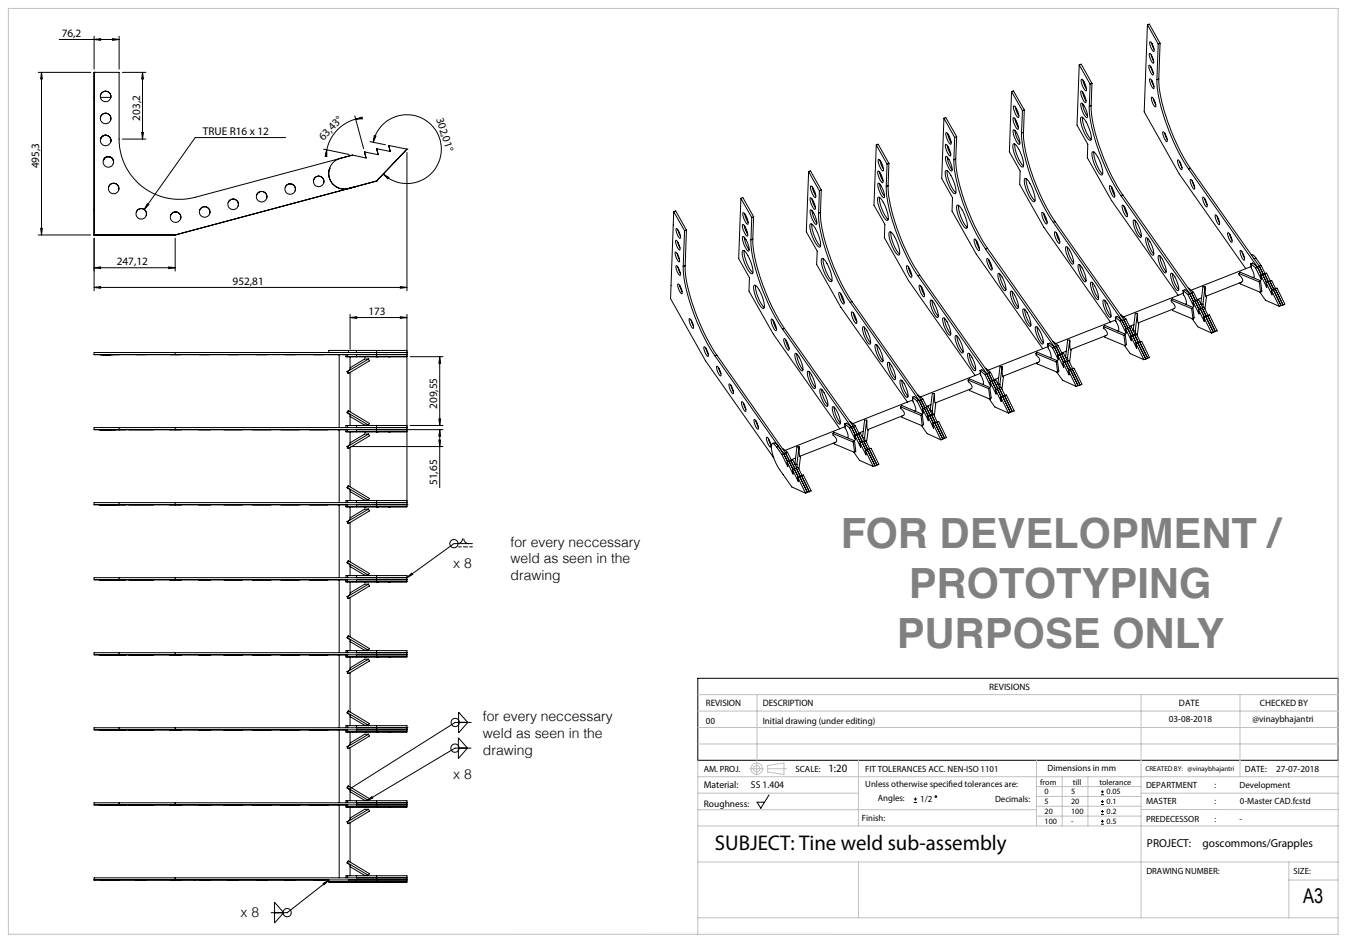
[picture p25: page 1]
TRUE R16 x 12; CHECKED BY; SUBJECT: Tine weld sub-assembly; PROJECT: goscommons/Grapples; Material: SS 1.404; DRAWING NUMBER:; AM. PROJ.; FIT TOLERANCES ACC. NEN-ISO 1101; Dimensions in mm; CREATED BY:; 0.5 Finish:; SCALE: 1:20; MASTER; 0-Master CAD.fcstd; FOR DEVELOPMENT / PURPOSE ONLY

for every neccessary
weld as seen in the
drawing

DESCRIPTION
Initial drawing (under editing)

Unless otherwise specied tolerances are:
Angles:

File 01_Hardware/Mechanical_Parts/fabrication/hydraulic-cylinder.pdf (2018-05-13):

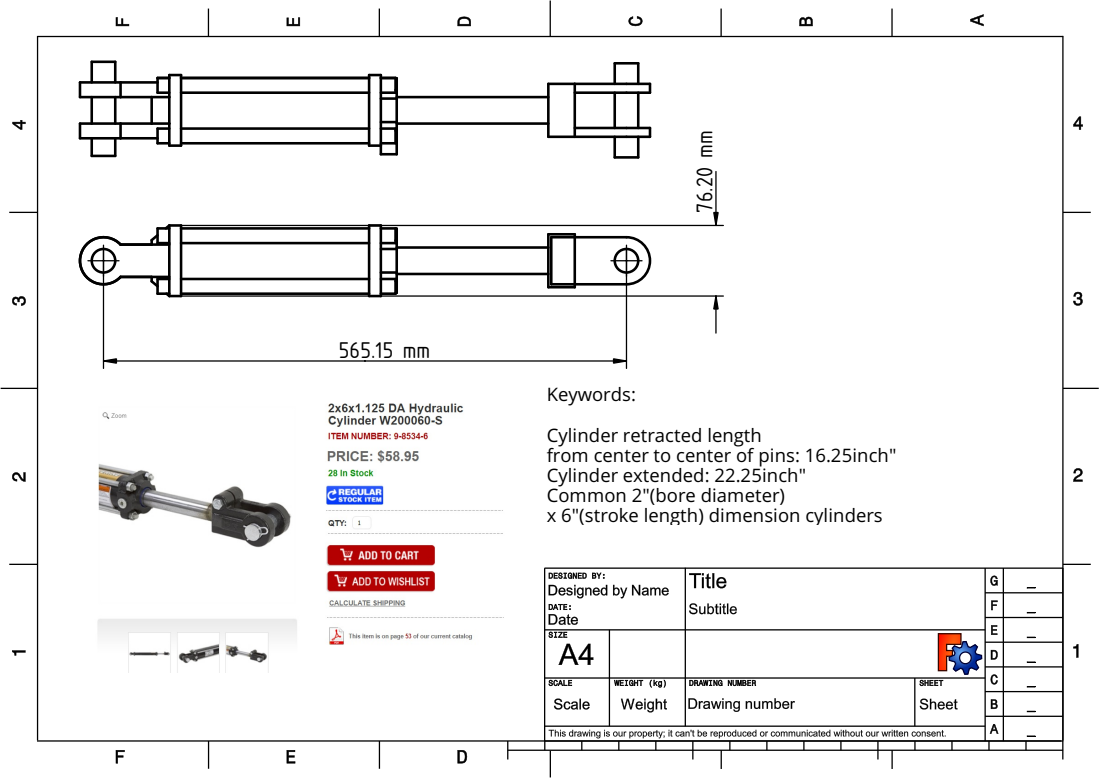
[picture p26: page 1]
Keywords:

Cylinder retracted length
from center to center of pins: 16.25inch" Cylinder extended: 22.25inch" Common 2"(bore diameter)

x 6"(stroke length) dimension cylinders

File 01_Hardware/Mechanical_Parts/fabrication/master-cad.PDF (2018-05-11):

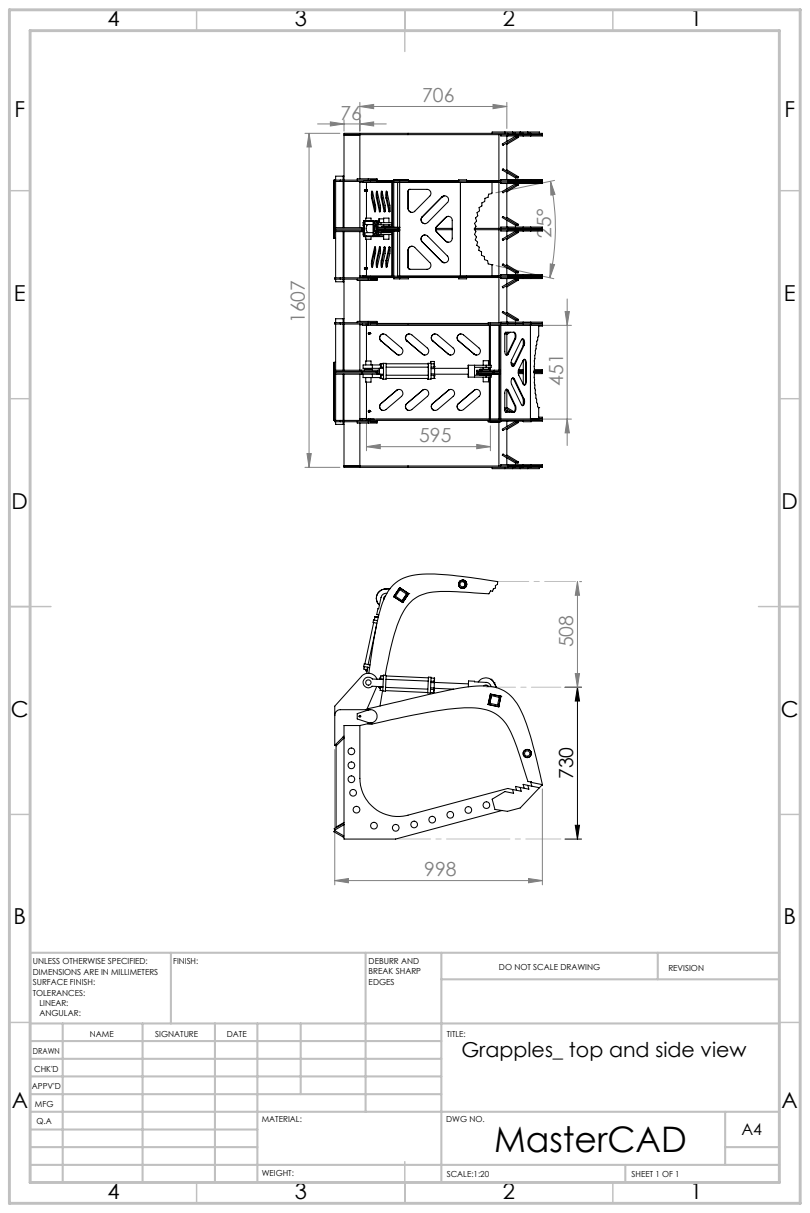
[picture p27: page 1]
FINISH:; DEBURR AND; BREAK SHARP; DO NOT SCALE DRAWING; REVISION; SCALE:1:20; SHEET 1 OF 1

UNLESS OTHERWISE SPECIFIED:
DIMENSIONS ARE IN MILLIMETERS
SURFACE FINISH:
TOLERANCES:
LINEAR:
ANGULAR:

NAME | SIGNATURE | DATE | | | | TITLE: Grapples_ top and side view

DRAWN
CHK'D
APPV'D
MFG
Q.A | | | | MATERIAL: | DWG NO. MasterCAD | A4

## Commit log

2018-05-08 added missing parts, update the assemblies
    [Lids Assembly.fcstd, Master CAD.fcstd, Outside tine.fcstd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]
2018-05-11 2D Drawing of Top and Side views
    The drawings are saved in DWG and PDF format. It was done in solidworks and I had issues opening it in FreeCAD
    [Drawing file.DWG]
2018-05-12 new tubing with all holes adjusted
    [Inside Gussets.fcstd, Inside tine.fcstd, Lid.fcstd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]
2018-05-12 organizing honomatology
    [Lid_Plate.fcstd, Lids Assembly.fcstd, Master CAD.fcstd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]
2018-05-12 Added Grapple CAD Structure.png
2018-05-12 honomatology organizing
    [Lids Assembly.fcstd, Master CAD.fcstd, Mount_Cylinder_base.fcstd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]
2018-05-13 Hydraulic cylinder tech drawing
    I was able with some difficulties to make a drawing of hydraylic cylinder with techdraw workbench but I was able, finally. I will try to make a demo example of what I have done so far. See the commit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
    1. Adding a drawing to the CAD file using techdraw workbench.
    1.2. Adding references and keywords for other users.
    2. Exporting to pdf; exporting to svg.
    3. Staging all the files related to this commit (CAD model, pdf, svg).
    4. Making the pull request.
    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
    [cylinder new extended.fcstd]
2018-05-13 Changed drawings to proper location
    [Drawing file.DWG]
2018-05-13 Started svg documentation
    @polemidis, is this a proper way of doing the svgs, or just the shape of the gusset?
    [master-cad.DWG]
2018-05-13 Complete svg for laser cut parts
2018-05-15 Added Grapple CAD Structure.jpg
2018-05-15 Relocation of files, to show readme
    The readme in the mechanical parts folder show a brief overview of how this section of the repository is organized. It helps users and contributors better understand what is in the folders and howto 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
    [Inside Gussets.fcstd, Inside tine.fcstd, Lid jaw.fcstd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]
2018-05-15 Added cad files to the CAD folder
    [Cylinder rod mount.fcstd, Lid.fcstd, Lids Assembly.fcstd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]
2018-05-15 Re ordering of CAD diles, Folders and readme
2018-05-16 Conflict solving
    A copied locally the files from the last master branch version into the tech-drawing branch. That should work.
    [Lids Assembly.fcstd, Master CAD.fcstd, Support Assembly.fcstd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]
2018-05-16 Revert "Conflict solving"
    This reverts commit 3b7e99b2cb255df6c64a2a177a88cff549184d53.
    [Lids Assembly.fcstd, Master CAD.fcstd, Support Assembly.fcstd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]
2018-05-16 Relocation of files to proper folder
    [Lid_Plate.fcstd, Master CAD.fcstd, Mount_Cylinder_base.fcstd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]
2018-05-16 Importing missing files after confict problem
    [Inside Gussets.fcstd, Inside tine.fcstd, Lid jaw.fcstd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]
2018-05-20 file names fix
    [cylinder base mount.fcstd]
2018-05-21 fix a dxf
    [Mount_Cylinder_base.fcstd, mount cylinder base plate inner.dxf]
2018-06-07 increase hole in tines where round tubing goes through so to have some clearance
    [Master CAD.fcstd, Outside tine.fcstd, Tines Assembly.fcstd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]
2018-06-20 changed the pin structure. Added bushings to the hinch. Tree file has to be updated
    [Master CAD.fcstd, Mount_Cylinder_base.fcstd, Support Assembly.fcstd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]
2018-07-03 improvments after the prototype. Some new bushings, new ssqa lpates, the whole grapple is 2in shorter, so the inside/outside tines are shorter, the lid are shorter too
    [Lid jaw.fcstd, Lid_Plate.fcstd, Lids Assembly.fcstd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]
2018-07-09 tube for lids goes all the way to the outer face. Lids have bigger holes to accept the tube, and brace plate lids are slightly smaller so they will fit and weld better
    [Lid_Plate.fcstd, Lids Assembly.fcstd, Master CAD.fcstd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]
2018-07-14 top square tubing is thicker. Extra plate on top of top square tubing. Changes on the cylinder mount base plate
    [0-Master CAD.fcstd, Master CAD.fcstd, Mount_Cylinder_base.fcstd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]
2018-07-18 minor touches to the top support plate
    [Support plate on top of square tubing.fcstd, support plate on top of square tubing.dxf]
2018-10-01 Parametrized position of tines on grapples
    [Master.scad, insidetine.dxf, outsidetine.dxf]
2018-10-01 Update of parametric model
    [Master.scad, hinch.dxf, mount_cylinder.dxf]
2018-10-02 Added gussets to in and out tynes
    [Master.scad, ingussets.dxf, outgussets.dxf]
2018-10-03 Added lid plates
    [Master.scad, brace_plate_lid.dxf]
2018-10-03 Added front and upper plates of lid assembly + gussets dfx files missing
    [Master.scad, brace_plate_lid_front.dxf, brace_plate_lid_upper.dxf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]
2018-10-03 added square tube. Modularized square tubes for easy reuse.
    [Master.scad]
2018-10-03 added lid jaw
    [Master.scad, lid_jaw.dxf]
2018-10-03 added two lids
    [Master.scad]
2018-10-03 Updated lids subassembly
    [Master.scad, cylinder_rod_mount.dxf, lid_plate.dxf]
2018-10-04 Added rod mount to lids assembly
    [Master.scad, cylinder_rod_mount_in.dxf]
2018-10-04 Re-organized folder
    I put the customizer files seperate from freeCAD files.
    [Master.scad, brace_plate_lid.dxf, brace_plate_lid_front.dxf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]
